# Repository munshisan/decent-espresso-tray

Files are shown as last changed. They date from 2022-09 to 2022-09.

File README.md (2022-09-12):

# decent-espresso-tray

This project contains files to print a waste tray and related parts to be used with [Decent Espresso's DE1](https://decentespresso.com) machine together with [Decent's bluetooth scale](https://decentespresso.com/decentscale).

## Motivation
The motivation for this project was [explained here](https://3.basecamp.com/3671212/buckets/7351439/messages/5296473889) but I'll copy/paste the relevant bits below.

> Headline: I've replaced the Decent drip tray with a 3D printed tray that sits above the Decent Scale (DS). This stackup has been working well for me -- from pulling shots by weight, to steaming milk, refilling water,  flushing/routine maintenance, etc. (My DE1 is not plumbed.)
> 
> Pros of this setup:
> * Brew by weight
> * Everything stays put nicely and looks neat
> * The scale is not exposed to liquids/steam
> * The static weight of everything above the scale (minus the SS tray cover) is about 130g
> * Slightly more headroom above the tray (useful for doing a pour-overs, say)

To summarize, this stackup allows the Decent Scale to sit beneath, fitted to, the new drip-tray, in a ready-to-brew configuration. The stackup can be easily moved ouf the way to refill the water tank and the tray can be easily removed and refitted to the scale for emptying or cleaning the former.

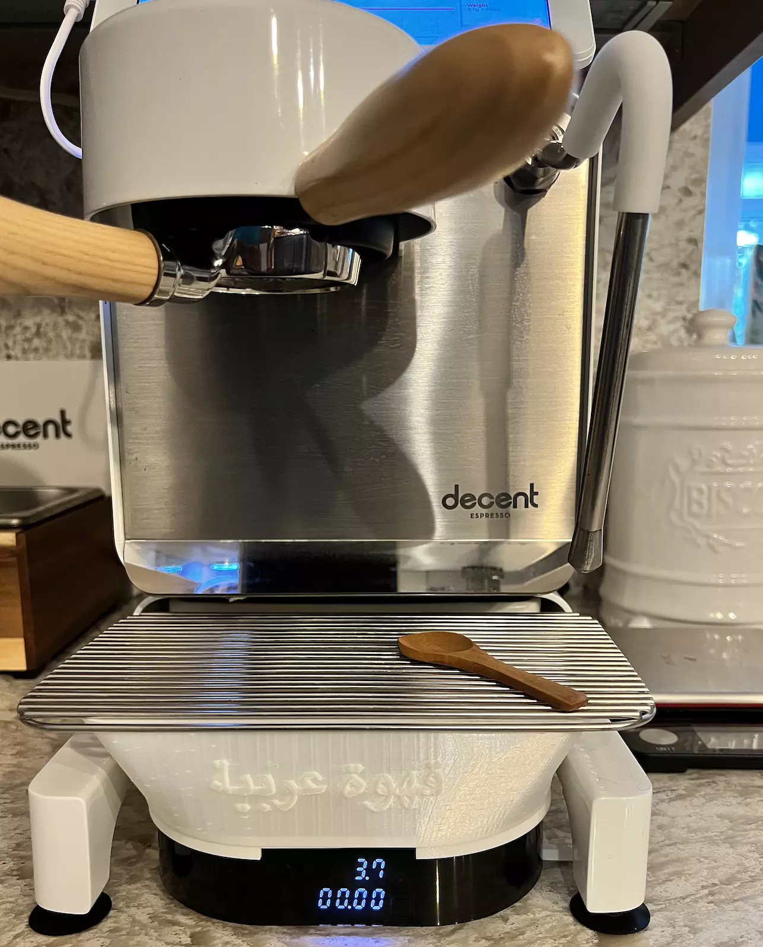
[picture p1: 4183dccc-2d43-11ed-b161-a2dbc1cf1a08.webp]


## How it works

The Decent Scale has a grippy, rubberized coating on its base to sit securely on most countertop surfaces.

In this stackup, the scale cover fits snugly[^1] over the scale and the tray is glued to the scale cover, making the whole stackup stay put on the counter.

[^1]: The scale cover should be printed in TPU95A or similar material that allows the scale cover to stretch around and grip the scale.

The wire guide (aka wire stent) is necessary when connecting the scale to USB power with the supplied cable as any physical contact interference between the cable and the scale's cover will produce erroneous readings. The wire guide moves the wire away from the scale to avoid interference.

The waste chute extends the waste discharge exit point to the front of the enclosure and thus over the drip tray, allowing the drip tray to capture all the discharge.

## How to print and assemble

[Click here for an illustration of the parts](https://github.com/munshisan/decent-espresso-tray/blob/main/Decent%20drip%20tray%20stackup.pdf)

### The Drip Tray
Use any non-porous material that is stable up to 150C. In my experience high temperature PLA works just fine. Nylon and polycarbonate would be equally suitable. The material need not be rigid but should not be overly flexible. Do not use CPE as it is porous. *Leak test your tray before proceeding.*

### The Scale Cover 
The STL is sized for TPU95A[^1] to provide a glove-like fit to the scale, yet not so snug that it remains easy to remove and re-install which is a frequent occurrence. TPU95A is a stretchy, rubber-like material. Glue the scale cover and drip tray together with a small amount of cyanoacrylate adhesive such as Krazy Glue.

### The Waste Chute Extender
Print this in nylon, CPE or similar flexible material. Depending on the print method, a little bit of trimming may be needed to clean up supports and left-over build plate adhesion material. *Ensure that the chute completely clear of any leftover print material.* Orient the waste chute extender so that the slot points down and sits over the drip tray. Carefully insert *just enough* of it into the waste chute port on the DE1 until the front edge of the waste chute extender reaches the lower edge of the mirror on the face of the DE1. Test that you haven't inserted it too far by running a shot or screen purge. The volume of the waste water purged should not be affected by the waste chute extender.

### Wire Guide
The wire guide is only necessary if using with USB power (highly recommended), and its only purpose is to guide the USB cable away from the scale so it does not interfere with the scale to prevent erroneous measurements. Firmly press-fit the wire guide with the flared end sitting over the right-angle USB connector's strain relief. Check that you don't have interference issues by wiggling the cable and watching the readout.

--- 
**A Parseeker**, September 2022

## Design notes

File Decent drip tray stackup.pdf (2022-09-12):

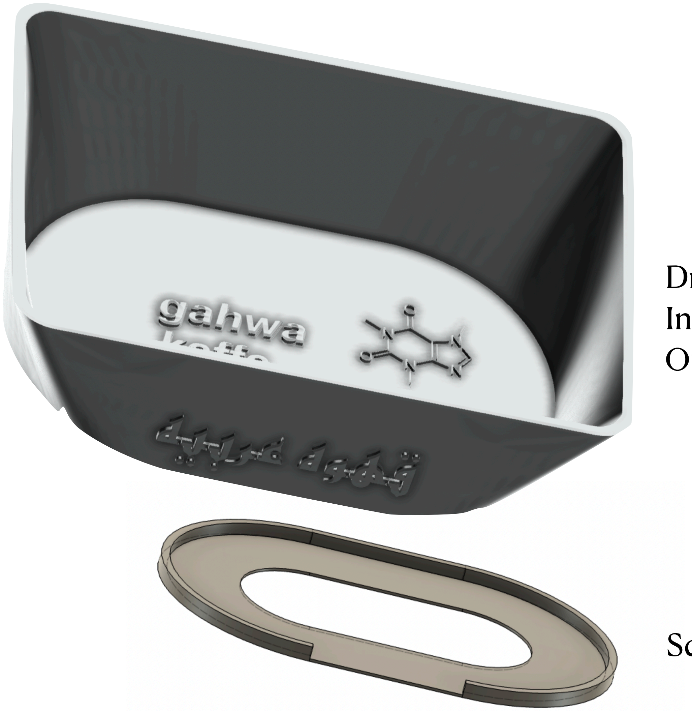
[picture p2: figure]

Scale cover (shown upside down)

Drip tray.
Inside graphics: text and caffeine molecule
Outside graphic: “coffee Arabica” in Arabic (of course!)

Waste chute extender

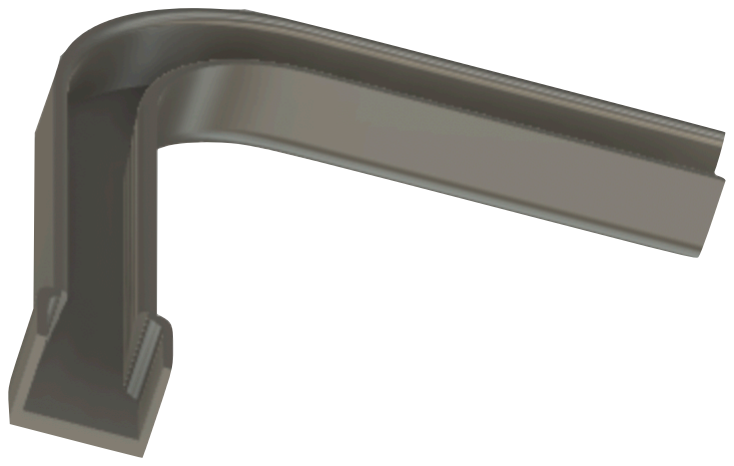
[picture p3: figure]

USB cable guide (the flared end fits over the cable’s strain relief)

# Decent DE1 & Scale Stackup

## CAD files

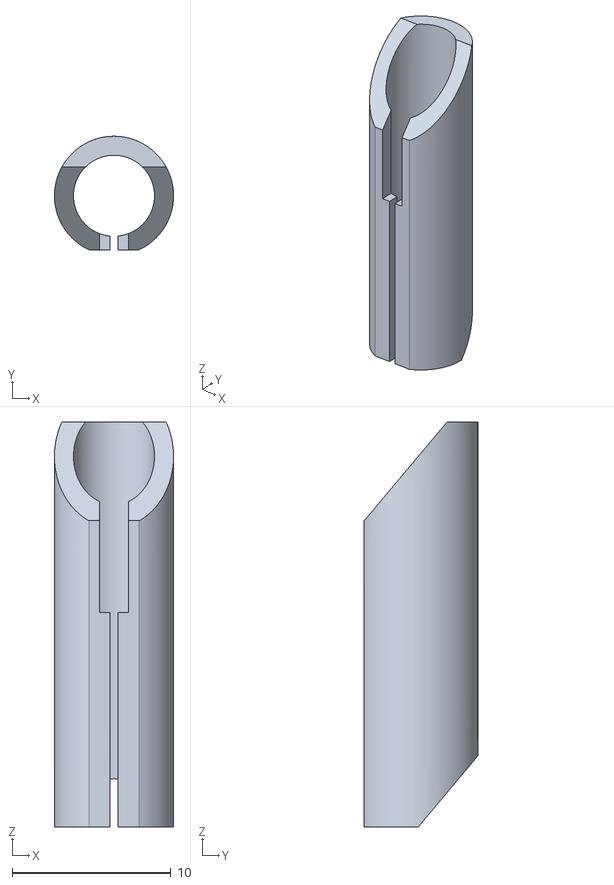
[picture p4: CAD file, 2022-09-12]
Waste-chute.stl
7.50 x 7.15 x 25.5

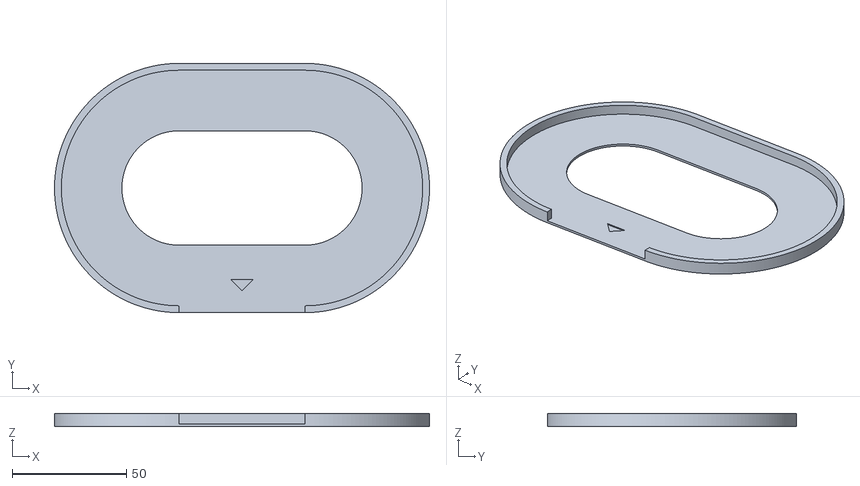
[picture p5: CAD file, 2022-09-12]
Scale-cover.stl
164.0 x 109.0 x 5.50

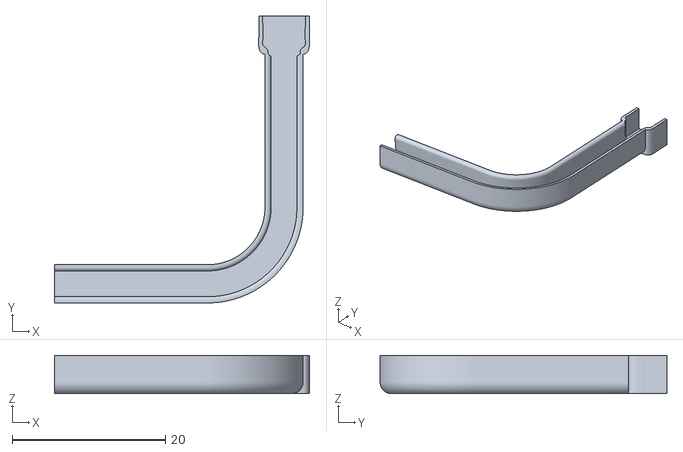
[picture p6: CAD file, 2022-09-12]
Wire-guide.stl
33.3 x 37.5 x 5.00

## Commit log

2022-09-12 Uploaded STL's
    [Scale-cover.stl, Waste-chute.stl, Wire-guide.stl]
2022-09-12 Update README.md
    Added print and assembly instructions.
